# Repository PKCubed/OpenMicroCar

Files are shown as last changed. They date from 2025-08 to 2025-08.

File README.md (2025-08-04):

# OpenMicroCar
An ESP32 based 4-motor vehicle designed as a single circuit board.

The idea here is to build 4 or more of these, and play a game of capture the flag with an analog FPV system on each little car. The IR leds and receivers will be used to "shoot" other cars laser-tag style. The ESP32s will use WiFi, or something else to communicate with a raspberry pi server. There will be two zones, one for each team, that are considered safe zones for that team, and will be another esp32 or esp8266 that has an IR receiver. When that receiver detects a car's infrared transmission, it knows it is in the safe zone. An opponent can drive into the safe zone of it's opposing team to capture its flag. It then has to get back to it's safe zone. If it is shot in the middle by the opponent, the flag is transferred to the car that shot it. They then have to bring it to their safe side. If a car gets shot, it must drive back to its safe zone before it can shoot or capture flags.

A car will be colored with its team color, orange or purple. When a car has a flag, the LEDs will blink in a fast pattern. When a car has been shot, its leds get dim and some leds fade red until it gets back to safety. When a car is shot, but is still in a safe zone, some leds will flash white and quickly fade back to the team color.

This tiny car has a PCB footprint of just 55 by 85.5 millimeters. The components all together cost under $30. It's designed to have 4 N20 motors soldered to the bottom, and held on by wrapping 2 lengths of wire around them and soldering to the PCB. Each motor has its own PWM control, as well as direction and braking control.

There are 12 infrared leds positioned around the car, all broadcasting the same signal from the ESP32 through a transistor. There are 2 IR receivers. One in the front designed to be the "shooting" receiver, and one in the back to alert the driver if they are being followed (may or may not get implemented).

There are also 12 WS2812b addressable RGB leds on each car. 8 facing down, and 4 facing up.

There is provision for a speaker and amplifier IC on board. This can be used to make beeps and boops, or maybe I'll try to output actual sampled sounds.

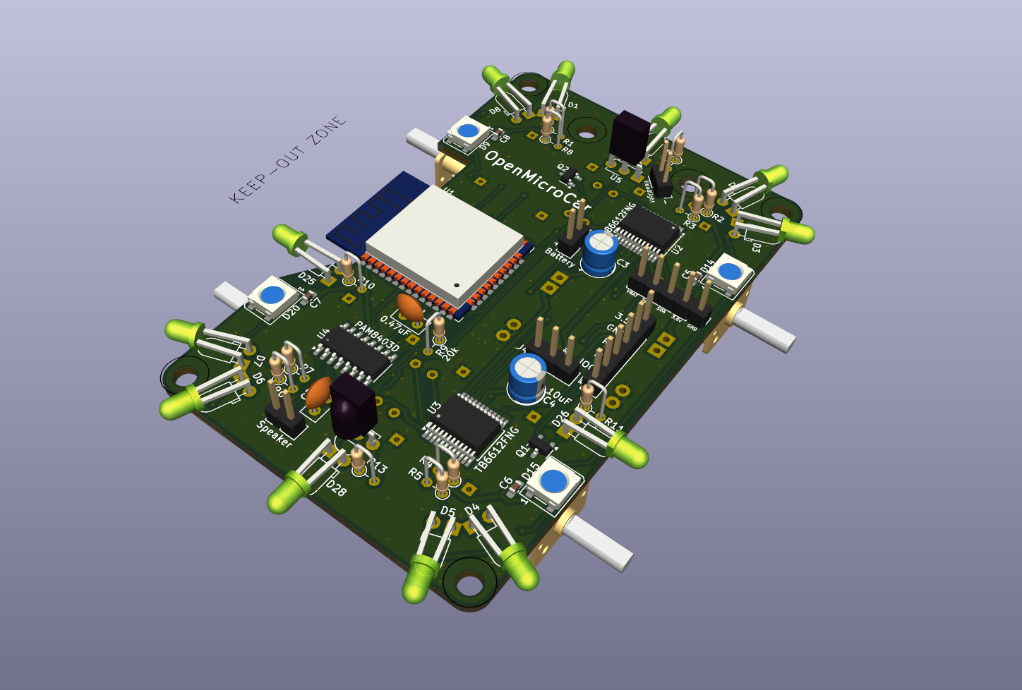
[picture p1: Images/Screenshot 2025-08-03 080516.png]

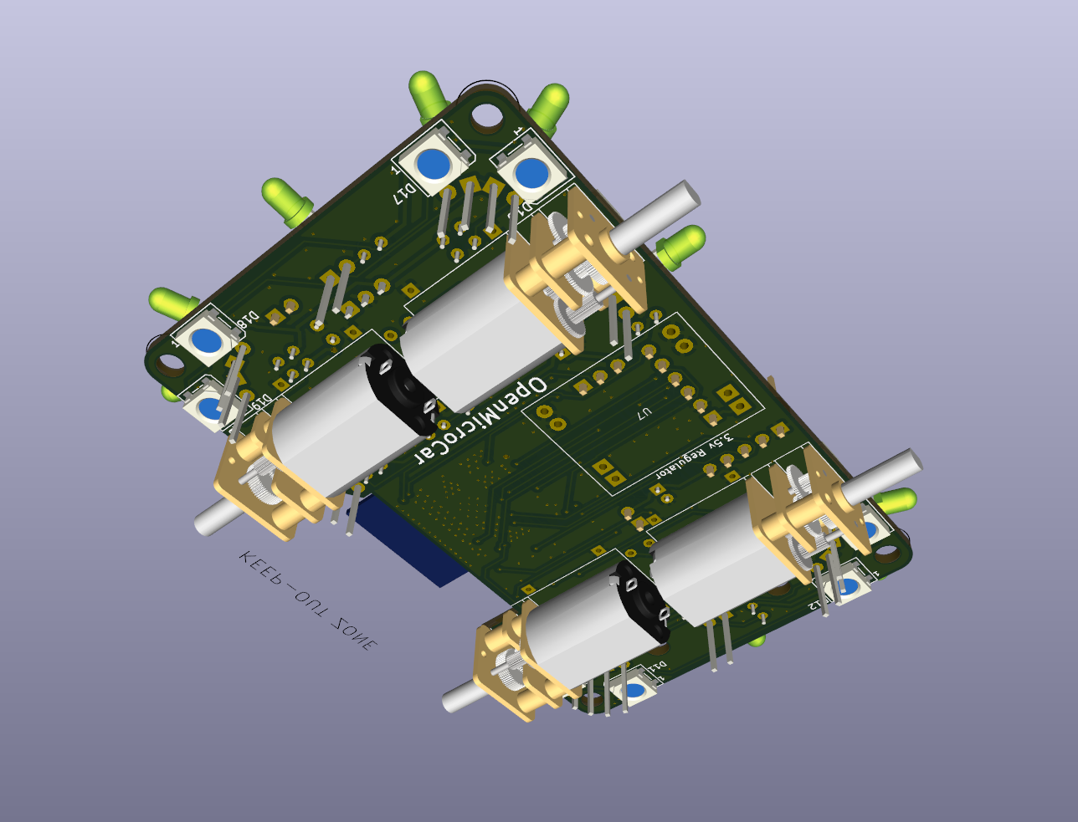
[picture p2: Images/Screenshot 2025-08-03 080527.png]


# Communication Details
Everything here is just my plans. Nothing has been actually tested and done yet.

Each car will be controlled through a web interface on people's phones. This web interface will come from a python program on a raspberry pi. When someone want's their car to go forward, they press the button on the web interface, which the python program sees, and then sends via wifi socket to the esp32 on that person's car, that they want to go forward. If the car doesn't hear from the python program for 1 second, it shuts off and goes to the disconnected failsafe state, that way it won't just drive away. We want the button latency to be as low as possible, approaching imperceptible.

Each car will send out a couple bytes through the IR leds that will let other cars know which car it is. This will be the car ID code.

People can also press the shoot button on their phone. This will tell the python program to request a shoot from the car. This will then read data through the IR receiver, and save any car ID codes it sees. It will report these back to python. At the same time, if the safe zone receivers see any IR car ID codes, Python will have seen that. If any of the shot cars match the safe cars, they will not be affected, but will be sent the safe shot signal to flash their LEDs and make a noise similar to that you get when you shoot a metal baloon in BTD Battles. If a car is not detected to be in a safe zone, it will be sent the shot signal, and it will be marked as shot until python sees it has been received by it's safe zone receiver.

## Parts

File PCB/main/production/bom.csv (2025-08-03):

Designator | Footprint | Quantity | Value | LCSC Part #
C1 | C_Disc_D5.0mm_W2.5mm_P2.50mm | 1 | 0.47uF
C2 | C_Disc_D5.0mm_W2.5mm_P2.50mm | 1 | 0.1uF
C3 | CP_Radial_D5.0mm_P2.00mm | 1 | 100uF
C4 | CP_Radial_D5.0mm_P2.00mm | 1 | 10uF
C5, C6, C7, C8 | 0603 | 4 | 0.1uF
D1, D25, D3, D5, D7 | Right Angle LED Reversed | 5 | LED
D10, D11, D12, D13, D14, D15, D16, D17, D18, D19, D20, D9 | LED_WS2812B_PLCC4_5.0x5.0mm_P3.2mm | 12 | WS2812B
D2, D26, D27, D28, D4, D6, D8 | Right Angle LED | 7 | LED
J1 | PinHeader_1x06_P2.54mm_Vertical | 1 | Conn_01x06_Pin
J2 | PinHeader_1x02_P2.54mm_Vertical | 1 | Headlight
J3 | PinHeader_1x05_P2.54mm_Vertical | 1 | Conn_01x05_Pin
J4 | PinHeader_1x03_P2.54mm_Vertical | 1 | Conn_01x03_Pin
J5 | PinHeader_1x02_P2.54mm_Vertical | 1 | Battery
LS1 | PinHeader_1x02_P2.54mm_Vertical | 1 | Speaker
M1, M2, M3, M4 | N20 Motor | 4 | ~
Q1, Q2 | SOT-23-3 | 2 | NPN
R1, R10, R11, R12, R13, R2, R3, R4, R5, R6, R7, R8 | R_Axial_DIN0204_L3.6mm_D1.6mm_P2.54mm_Vertical | 12 | 100
R9 | R_Axial_DIN0204_L3.6mm_D1.6mm_P2.54mm_Vertical | 1 | 20k
U1 | ESP32-WROOM-32 | 1 | ESP32-WROOM-32
U2, U3 | SSOP-24_5.3x8.2mm_P0.65mm | 2 | TB6612FNG
U4 | SOP-16_3.9x9.9mm_P1.27mm | 1 | PAM8403D
U5, U6 | Vishay_MINICAST-3Pin | 2 | TSDP341xx
U7 | DC Buck Converter | 1 | ~

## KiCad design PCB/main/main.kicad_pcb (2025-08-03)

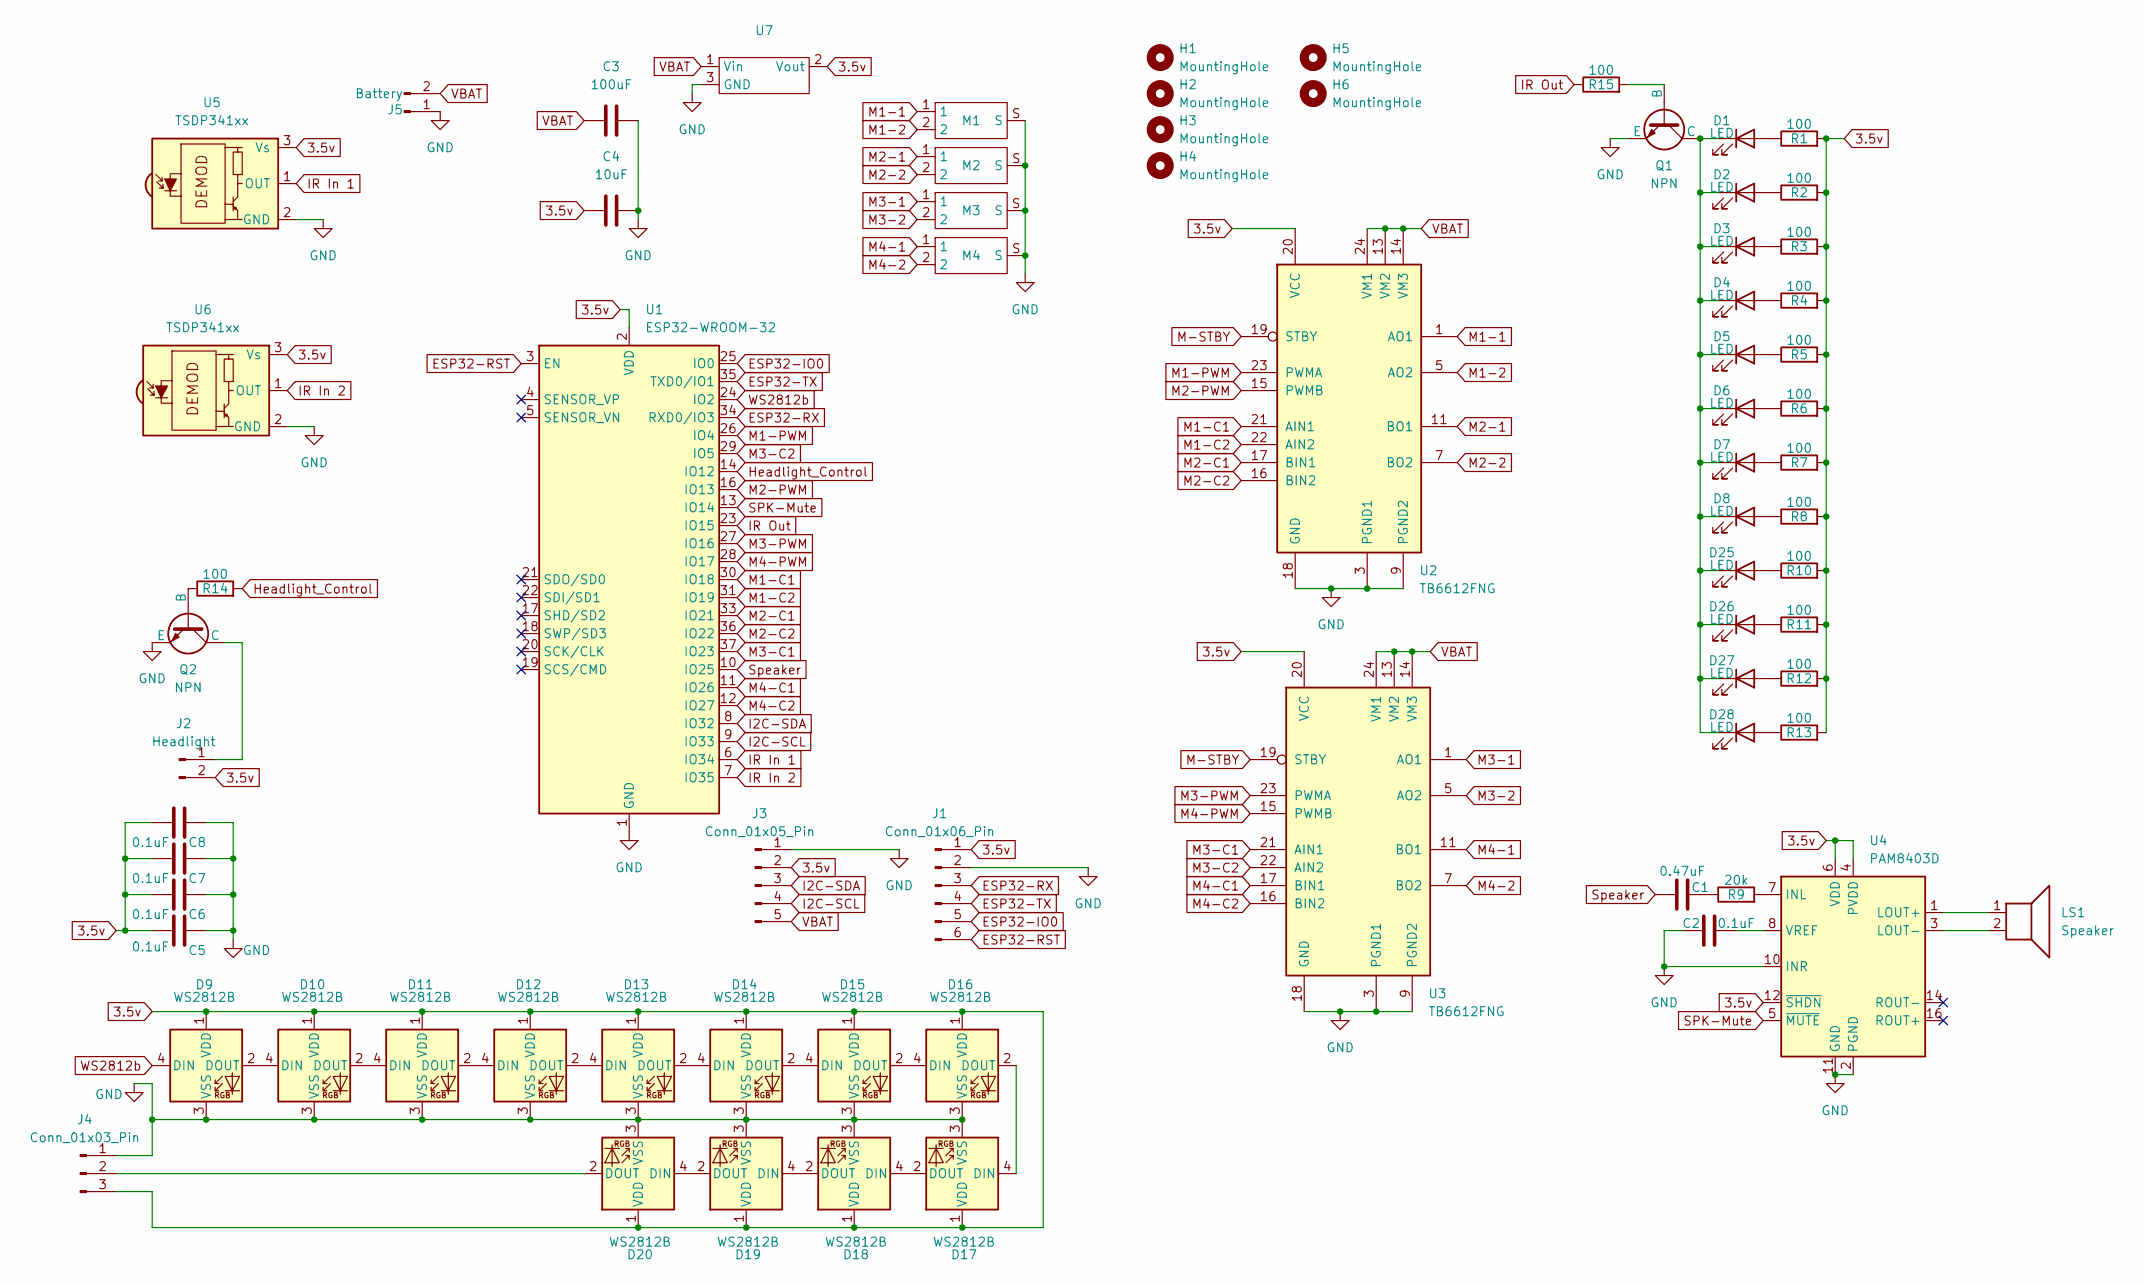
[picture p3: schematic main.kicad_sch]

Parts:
C1: 0.47uF; C_Disc_D5.0mm_W2.5mm_P2.50mm
C2: 0.1uF; C_Disc_D5.0mm_W2.5mm_P2.50mm
C3: 100uF; CP_Radial_D5.0mm_P2.00mm
C4: 10uF; CP_Radial_D5.0mm_P2.00mm
C5, C6, C7, C8: 0.1uF; C_0603_1608Metric_Pad1.08x0.95mm_HandSolder
D1, D3, D5, D7, D25: LED; Right Angle LED Reversed
D2, D4, D6, D8, D26, D27, D28: LED; Right Angle LED
D9, D10, D11, D12, D13, D14, D15, D16, D17, D18, D19, D20: WS2812B; LED_WS2812B_PLCC4_5.0x5.0mm_P3.2mm
H1, H2, H3, H4, H5, H6: MountingHole; MountingHole_3.2mm_M3
J1: Conn_01x06_Pin; PinHeader_1x06_P2.54mm_Vertical
J2: Headlight; PinHeader_1x02_P2.54mm_Vertical
J3: Conn_01x05_Pin; PinHeader_1x05_P2.54mm_Vertical
J4: Conn_01x03_Pin; PinHeader_1x03_P2.54mm_Vertical
J5: Battery; PinHeader_1x02_P2.54mm_Vertical
LS1: Speaker; PinHeader_1x02_P2.54mm_Vertical
M1, M2, M3, M4: N20 Motor
Q1, Q2: NPN; SOT-23-3
R1, R2, R3, R4, R5, R6, R7, R8, R10, R11, R12, R13: 100; R_Axial_DIN0204_L3.6mm_D1.6mm_P2.54mm_Vertical
R9: 20k; R_Axial_DIN0204_L3.6mm_D1.6mm_P2.54mm_Vertical
R14, R15: 100; R_0805_2012Metric_Pad1.20x1.40mm_HandSolder
U1: ESP32-WROOM-32
U2, U3: TB6612FNG; SSOP-24_5.3x8.2mm_P0.65mm
U4: PAM8403D; SOP-16_3.9x9.9mm_P1.27mm
U5, U6: TSDP341xx; Vishay_MINICAST-3Pin
U7: DC Buck Converter

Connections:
3.5v: C4.1, C5.2, C6.2, C7.2, C8.2, D9.1 (VDD), D10.1 (VDD), D11.1 (VDD), D12.1 (VDD), D13.1 (VDD), D14.1 (VDD), D15.1 (VDD), D16.1 (VDD), D17.1 (VDD), D18.1 (VDD), D19.1 (VDD), D20.1 (VDD), J1.1, J2.2, J3.2, J4.3, R1.2, R2.2, R3.2, R4.2, R5.2, R6.2, R7.2, R8.2, R10.2, R11.2, R12.2, R13.2, U1.2 (VDD), U2.20 (VCC), U3.20 (VCC), U4.4 (PVDD), U4.6 (VDD), U4.12 (~SHDN), U4.13 (PVDD), U5.3 (Vs), U6.3 (Vs), U7.2 (Vout)
ESP32-IO0: J1.5, U1.25 (IO0)
ESP32-RST: J1.6, U1.3 (EN)
ESP32-RX: J1.3, U1.34 (RXD0/IO3)
ESP32-TX: J1.4, U1.35 (TXD0/IO1)
GND: C2.1, C3.2, C4.2, C5.1, C6.1, C7.1, C8.1, D9.3 (VSS), D10.3 (VSS), D11.3 (VSS), D12.3 (VSS), D13.3 (VSS), D14.3 (VSS), D15.3 (VSS), D16.3 (VSS), D17.3 (VSS), D18.3 (VSS), D19.3 (VSS), D20.3 (VSS), J1.2, J3.1, J4.1, J5.1, M1.S, M2.S, M3.S, M4.S, Q1.3 (E), Q2.3 (E), U1.1 (GND), U1.15 (GND), U1.38 (GND), U1.39 (GND), U2.3 (PGND1), U2.4 (PGND1), U2.9 (PGND2), U2.10 (PGND2), U2.18 (GND), U3.3 (PGND1), U3.4 (PGND1), U3.9 (PGND2), U3.10 (PGND2), U3.18 (GND), U4.2 (PGND), U4.10 (INR), U4.11 (GND), U4.15 (PGND), U5.2 (GND), U6.2 (GND), U7.3 (GND)
Headlight_Control: R14.2, U1.14 (IO12)
I2C-SCL: J3.4, U1.9 (IO33)
I2C-SDA: J3.3, U1.8 (IO32)
IR In 1: U1.6 (IO34), U5.1 (OUT)
IR In 2: U1.7 (IO35), U6.1 (OUT)
IR Out: R15.1, U1.23 (IO15)
M1-1: M1.1, U2.1 (AO1), U2.2 (AO1)
M1-2: M1.2, U2.5 (AO2), U2.6 (AO2)
M1-C1: U1.30 (IO18), U2.21 (AIN1)
M1-C2: U1.31 (IO19), U2.22 (AIN2)
M1-PWM: U1.26 (IO4), U2.23 (PWMA)
M2-1: M2.1, U2.11 (BO1), U2.12 (BO1)
M2-2: M2.2, U2.7 (BO2), U2.8 (BO2)
M2-C1: U1.33 (IO21), U2.17 (BIN1)
M2-C2: U1.36 (IO22), U2.16 (BIN2)
M2-PWM: U1.16 (IO13), U2.15 (PWMB)
M3-1: M3.1, U3.1 (AO1), U3.2 (AO1)
M3-2: M3.2, U3.5 (AO2), U3.6 (AO2)
M3-C1: U1.37 (IO23), U3.21 (AIN1)
M3-C2: U1.29 (IO5), U3.22 (AIN2)
M3-PWM: U1.27 (IO16), U3.23 (PWMA)
M4-1: M4.1, U3.11 (BO1), U3.12 (BO1)
M4-2: M4.2, U3.7 (BO2), U3.8 (BO2)
M4-C1: U1.11 (IO26), U3.17 (BIN1)
M4-C2: U1.12 (IO27), U3.16 (BIN2)
M4-PWM: U1.28 (IO17), U3.15 (PWMB)
M-STBY: U2.19 (STBY), U3.19 (STBY)
unnamed: C1.2, R9.1
unnamed: D1.2 (A), R1.1
unnamed: D1.1 (K), D2.1 (K), D3.1 (K), D4.1 (K), D5.1 (K), D6.1 (K), D7.1 (K), D8.1 (K), D25.1 (K), D26.1 (K), D27.1 (K), D28.1 (K), Q1.1 (C)
unnamed: D2.2 (A), R2.1
unnamed: D3.2 (A), R3.1
unnamed: D4.2 (A), R4.1
unnamed: D5.2 (A), R5.1
unnamed: D6.2 (A), R6.1
unnamed: D7.2 (A), R7.1
unnamed: D8.2 (A), R8.1
unnamed: D9.2 (DOUT), D10.4 (DIN)
unnamed: D10.2 (DOUT), D11.4 (DIN)
unnamed: D11.2 (DOUT), D12.4 (DIN)
unnamed: D12.2 (DOUT), D13.4 (DIN)
unnamed: D13.2 (DOUT), D14.4 (DIN)
unnamed: D14.2 (DOUT), D15.4 (DIN)
unnamed: D15.2 (DOUT), D16.4 (DIN)
unnamed: D16.2 (DOUT), D17.4 (DIN)
unnamed: D17.2 (DOUT), D18.4 (DIN)
unnamed: D18.2 (DOUT), D19.4 (DIN)
unnamed: D19.2 (DOUT), D20.4 (DIN)
unnamed: D20.2 (DOUT), J4.2
unnamed: D25.2 (A), R10.1
unnamed: D26.2 (A), R11.1
unnamed: D27.2 (A), R12.1
unnamed: D28.2 (A), R13.1
unnamed: J2.1, Q2.1 (C)
unnamed: Q1.2 (B), R15.2
unnamed: Q2.2 (B), R14.1
unnamed: R9.2, U4.7 (INL)
unnamed: LS1.1, U4.1 (LOUT+)
unnamed: LS1.2, U4.3 (LOUT-)
unnamed: C2.2, U4.8 (VREF)
SPK-Mute: U1.13 (IO14), U4.5 (~MUTE)
Speaker: C1.1, U1.10 (IO25)
VBAT: C3.1, J3.5, J5.2, U2.13 (VM2), U2.14 (VM3), U2.24 (VM1), U3.13 (VM2), U3.14 (VM3), U3.24 (VM1), U7.1 (Vin)
WS2812b: D9.4 (DIN), U1.24 (IO2)

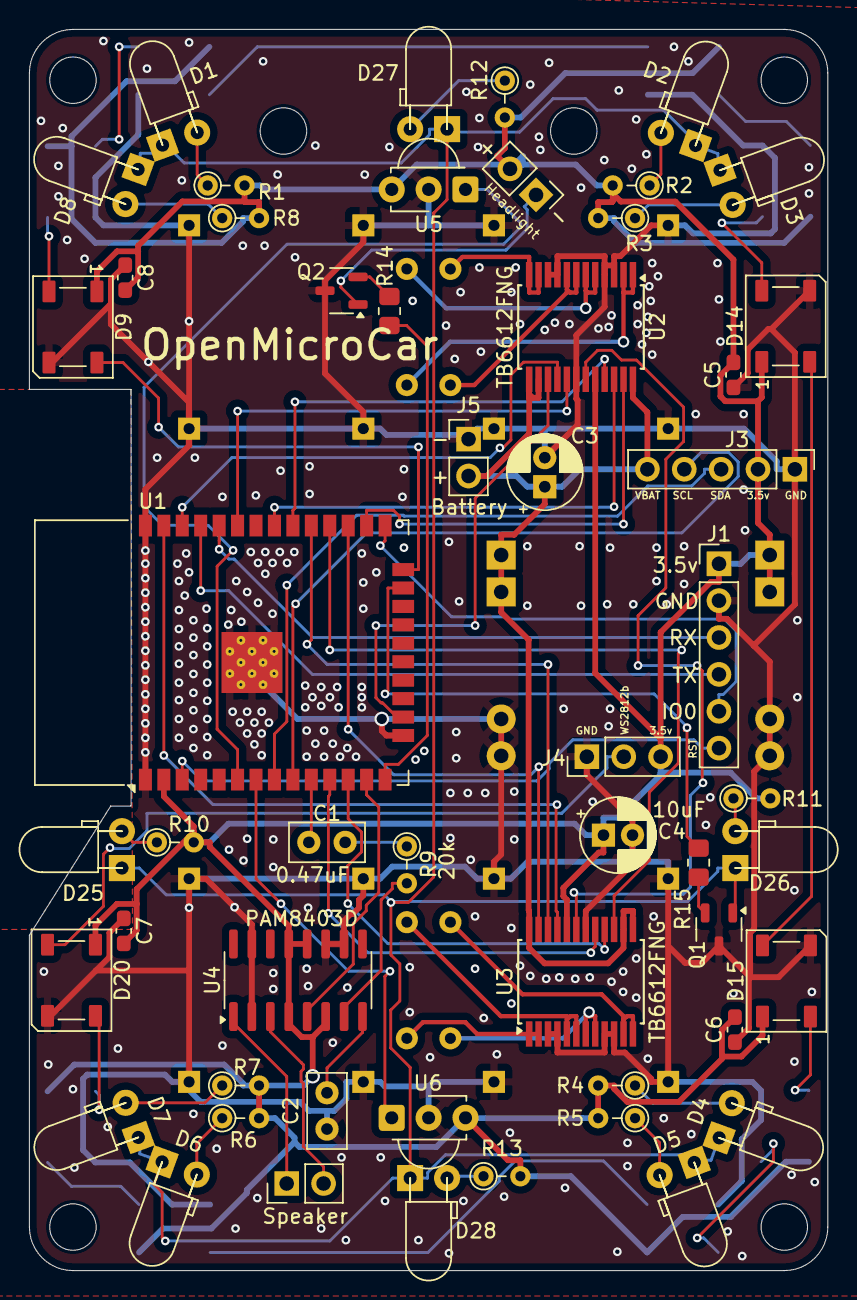
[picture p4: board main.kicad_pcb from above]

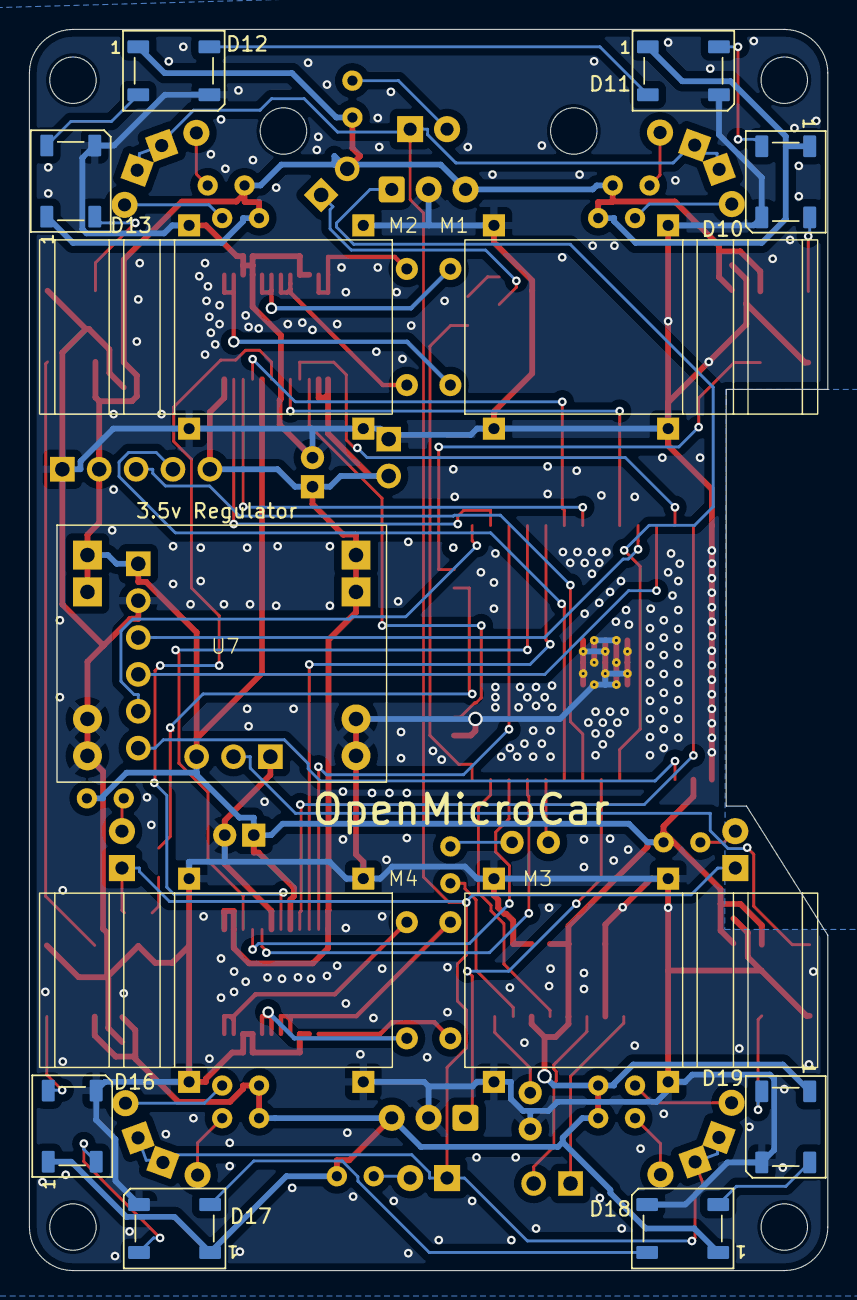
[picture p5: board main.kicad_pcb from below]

Board: 2 copper layers, 55.0 x 85.5 mm, 72 parts (13 on the bottom side), 70 nets.

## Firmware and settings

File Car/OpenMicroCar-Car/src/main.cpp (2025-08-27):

#include <WiFi.h>
#include <IRremoteESP8266.h>
#include <IRrecv.h>
#include <IRsend.h>
#include <IRutils.h>

#define FL_PIN 26
#define BL_PIN 14
#define FR_PIN 12
#define BR_PIN 13
#define SH_PIN 25

// --- WiFi Configuration ---
const char* ssid = "OpenMicroCar";
const char* password = "vroomvroom";
const char* serverIp = "192.168.77.2"; 
const int serverPort = 5000;

// --- Static IP Configuration ---
// Adjust these values for your specific network
IPAddress staticIP(192, 168, 77, 51);
IPAddress gateway(192, 168, 77, 1);
IPAddress subnet(255, 255, 255, 0);

WiFiClient client;

// --- Car and IR Configuration ---
const long CAR_IR_ADDRESS = 0x01; 

const int IR_EMITTER_PIN = 4;   // Pin connected to the IR LED
const int IR_RECEIVER_PIN = 27; // Pin connected to the IR receiver's OUT pin

IRsend irsend(IR_EMITTER_PIN);
IRrecv irrecv(IR_RECEIVER_PIN);
decode_results results;

// --- Game State Variables ---
bool is_disabled = false;
unsigned long lastIrBroadcast = 0;
const int IR_BROADCAST_INTERVAL = 500; // milliseconds

int shoot_timer = 0;

// --- Functions ---
void connectToServer() {
  if (client.connect(serverIp, serverPort)) {
    Serial.println("Connected to server!");
  } else {
    Serial.println("Connection failed. Retrying in 5 seconds...");
    delay(5000);
  }
}

void sendData(String data) {
  if (client.connected()) {
    client.print(data);
  } else {
    Serial.println("Client not connected. Data not sent.");
    connectToServer(); // Try to reconnect
  }
}

void handleServerCommands() {
  if (client.available()) {
    String server_command = client.readStringUntil('\n');
    Serial.print("Received server command: ");
    Serial.println(server_command);

    if (server_command.length() == 4) {
      long command_address = strtol(server_command.substring(0, 2).c_str(), NULL, 16);
      long command_value = strtol(server_command.substring(2, 4).c_str(), NULL, 16);

      if (command_address == 0x80) { 
        if (command_value == 0x01) {
          is_disabled = true;
          Serial.println("SERVER COMMAND: Car has been disabled!");
        } else if (command_value == 0x02) {
          is_disabled = false;
          Serial.println("SERVER COMMAND: Car has been re-enabled!");
        }
      } else if (command_address == 0x02) {
        if (command_value == 0x01) {
          digitalWrite(FL_PIN, 1);
          digitalWrite(FR_PIN, 1);
          digitalWrite(BL_PIN, 0);
          digitalWrite(BR_PIN, 0);
        } else if (command_value == 0x02) {
          digitalWrite(FL_PIN, 0);
          digitalWrite(FR_PIN, 0);
          digitalWrite(BL_PIN, 1);
          digitalWrite(BR_PIN, 1);
        } else if (command_value == 0x03) {
          digitalWrite(FL_PIN, 0);
          digitalWrite(FR_PIN, 1);
          digitalWrite(BL_PIN, 1);
          digitalWrite(BR_PIN, 0);
        } else if (command_value == 0x04) {
          digitalWrite(FL_PIN, 1);
          digitalWrite(FR_PIN, 0);
          digitalWrite(BL_PIN, 0);
          digitalWrite(BR_PIN, 1);
        } else if (command_value == 0x05) {
          digitalWrite(FL_PIN, 0);
          digitalWrite(FR_PIN, 0);
          digitalWrite(BL_PIN, 0);
          digitalWrite(BR_PIN, 0);
        }
      } else if (command_address == 0x03) {
        if (command_value == 0x01) {
          shoot_timer = millis();
        }
      }
    }
  }
}

void setup() {
  Serial.begin(115200);

  pinMode(FL_PIN, OUTPUT);
  pinMode(FR_PIN, OUTPUT);
  pinMode(BL_PIN, OUTPUT);
  pinMode(BR_PIN, OUTPUT);
  pinMode(SH_PIN, OUTPUT);

  randomSeed(analogRead(0));

  WiFi.config(staticIP, gateway, subnet);

  delay(100);

  // Connect to WiFi
  Serial.println("Connecting to WiFi...");
  WiFi.begin(ssid, password);
  while (WiFi.status() != WL_CONNECTED) {
    delay(500);
    Serial.print(".");
  }
  Serial.println("\nConnected to WiFi!");
  Serial.print("IP Address: ");
  Serial.println(WiFi.localIP());

  // Initialize the IR receiver and sender using the IRremoteESP8266 API
  irrecv.enableIRIn(); // This is the old API, but it's used for this library
  irsend.begin();
  Serial.println("IR system enabled.");

  connectToServer();
}

uint32_t NECCode(uint8_t address, uint8_t command) {
  uint32_t necCode = 0;

  // Find the bitwise NOT of the address and command
  uint8_t address_inv = ~address; 
  uint8_t command_inv = ~command;
  necCode |= (uint32_t)address << 24;
  necCode |= (uint32_t)address_inv << 16;
  necCode |= (uint32_t)command << 8;
  necCode |= (uint32_t)command_inv << 0;

  return necCode;
}

void loop() {
  unsigned long currentTime = millis();

  if (shoot_timer + 100 > millis()) {
    digitalWrite(SH_PIN, 1);
  } else {
    digitalWrite(SH_PIN, 0);
  }

  // --- Task 1: Broadcast our own IR address ---
  if (currentTime - lastIrBroadcast > IR_BROADCAST_INTERVAL + random(0,100) && !is_disabled) { // The random function adds up to a 100ms jitter to hopefully prevent IR collisions. Each transmission will take about 70 ms, so collisions are very probable.
    irsend.send(NEC, NECCode(CAR_IR_ADDRESS,0), 32);
    lastIrBroadcast = currentTime;
  }

  // --- Task 2: Listen for and process incoming IR signals ---
  if (irrecv.decode(&results)) {
    // The IRremoteESP8266 library returns protocol types slightly differently
    if (results.decode_type == NEC) {
      long seenIrAddress = results.value;
      Serial.print("Received NEC Address: ");
      Serial.println(seenIrAddress, HEX);

      char hex_buffer[3];
      sprintf(hex_buffer, "%02X", seenIrAddress);
      
      String message = "CAR_SEEN:";
      message += hex_buffer;
      message += "\n";
      
      sendData(message);
    }
    irrecv.resume();
  }
  
  // --- Task 3: Handle commands from the server ---
  handleServerCommands();

  // --- Main Car Logic ---
  if (!is_disabled) {
    // Car is enabled, run motors, etc.
  } else {
    // Car is disabled, stop motors, etc.
  }
  
  if (!client.connected()) {
    connectToServer();
  }
}

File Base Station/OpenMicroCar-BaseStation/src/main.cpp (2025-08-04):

#include <Arduino.h>
#include <IRremoteESP8266.h>
#include <IRrecv.h>
#include <IRutils.h>
#include <ESP8266WiFi.h>

// Initialize Wifi Stuff
  const char* ssid = "OpenMicroCar";
  const char* password = "vroomvroom";

  // Set your static IP address
  IPAddress staticIP(192, 168, 77, 11); // For example: 192.168.1.100
  IPAddress gateway(192, 168, 0, 1);    // For example: 192.168.1.1 (your router's IP)
  IPAddress subnet(255, 255, 0, 0);   // Subnet mask
  IPAddress dns1(8, 8, 8, 8);           // Google's primary DNS server
  IPAddress dns2(8, 8, 4, 4);           // Google's secondary DNS server
  WiFiClient client;

  // Server details
  const char* serverIp = "192.168.77.2"; // <-- Change this to your computer's IP address
  const int serverPort = 5000;          // <-- The port your Python server will listen on



// Initialize IR Stuff
  const int RECV_PIN = 2;  // Define the pin connected to the IR receiver signal line
  IRrecv irrecv(RECV_PIN);
  decode_results results;
  struct NecCodeData {
    uint8_t address;
    uint8_t command;
  };

  NecCodeData received_data;

NecCodeData decodeNecCode(uint32_t necCode) { // Convert the Nec encoded address and data to integers
  NecCodeData decodedData;
  decodedData.address = (necCode >> 24) & 0xFF;
  decodedData.command = (necCode >> 8) & 0xFF;
  return decodedData;
}

void setup() {
  Serial.begin(115200);  // Initialize the serial console

  // Print initial message
  Serial.println();
  Serial.println("Connecting to WiFi with static IP...");

  // Configure WiFi with static IP
  WiFi.config(staticIP, gateway, subnet, dns1, dns2);
  
  // Connect to the WiFi network
  WiFi.begin(ssid, password);

  // Wait for connection
  while (WiFi.status() != WL_CONNECTED) {
    delay(500);
    Serial.print(".");
  }

  // Connection successful
  Serial.println("");
  Serial.println("WiFi connected!");
  Serial.print("Assigned IP Address: ");
  Serial.println(WiFi.localIP());

  irrecv.enableIRIn();   // Start the IR receiver
  Serial.println("IR receiver enabled. Listening for NEC protocol signals...");
}

void loop() {
  if (client.connected()) { // If we are connected to the server
    if (irrecv.decode(&results)) {
      // Check if the decoded protocol is NEC
      if (results.decode_type == NEC) {
        received_data = decodeNecCode(results.value);
        
        client.printf("BS_SEEN:%02X\n", received_data.address);
        Serial.printf("Received: %02X%02X\n", received_data.address, received_data.command);
      } else {
        // If it's not NEC, you can print a message to the console
        Serial.println("X");
      }
      // Resume receiving the next IR signal
      irrecv.resume();
    }
  } else { // If we are not connected to the server
    Serial.print("Connecting to server at ");
    Serial.print(serverIp);
    Serial.print(":");
    Serial.println(serverPort);

    // Try to connect to the server
    if (client.connect(serverIp, serverPort)) {
      Serial.println("Connected to server!");
    } else {
      Serial.println("Connection failed. Retrying in 1 seconds...");
      // Wait before retrying
      delay(1000);
      return;
    }
  }
}

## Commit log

2025-08-03 Uploaded PCB Files
    This is the first version of the PCB I designed yesterday.
    [bom.csv, designators.csv, main.kicad_pcb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]
2025-08-03 Base Resistors and README.md
    Added base resistors to the headlight and IR led transistors (facepalm), and added to the main README.md.
    [main.kicad_pcb, main.kicad_sch]
2025-08-04 Initial Code
    Initial Coding. Waiting for PCBs to arrive for more development.
2025-08-27 added basic motor test
